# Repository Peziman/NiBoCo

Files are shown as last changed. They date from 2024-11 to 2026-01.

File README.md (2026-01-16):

# NiBoCo
Boardcomputer and controller for a CWA pump for my Nissan Micra GA16DE project

# Why
I installed a GA16DE engine from a Nissan Almera in a Nissan Micra K11 1.0. Since this engine is much larger, there was no room for the V-belt drive of the water pump. Cutting out the frame was not an option for me, so the cooling system had to be converted to an electric pump. I chose a Pierburg CWA200 water pump, which is installed in some BMWs.

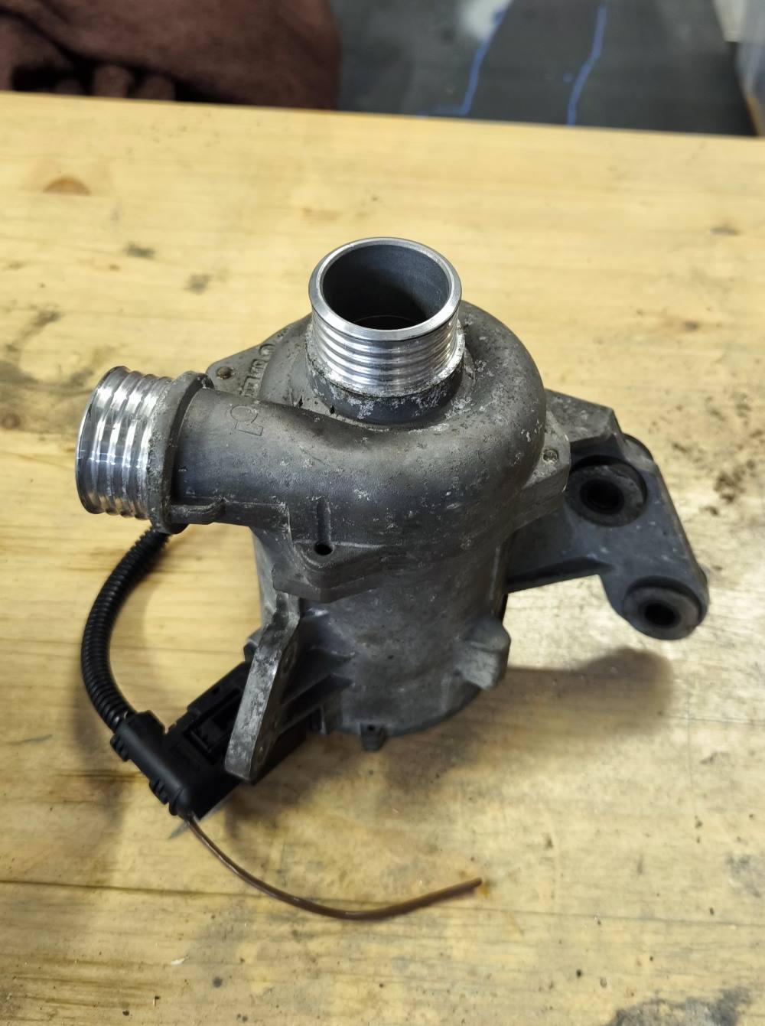
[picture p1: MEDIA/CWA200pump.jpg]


I also wanted to have an additional display in my speedometer for my Speeduino.
MielArrojado's project "speeduino-ardugauge" is just perfect.

https://github.com/MielArrojado/speeduino-ardugauge

So why not combine the two?

**This is a standalone version! There's no connection to Speeduino!**

# How is the cooling system set up?

Since there was no room for the belt drive of the water pump due to space constraints, and cutting into the frame for legal reasons was avoided, an electric coolant pump from BMW, an external thermostat from a Fiat 126, and a VW secondary pump for the heating circuit are used.

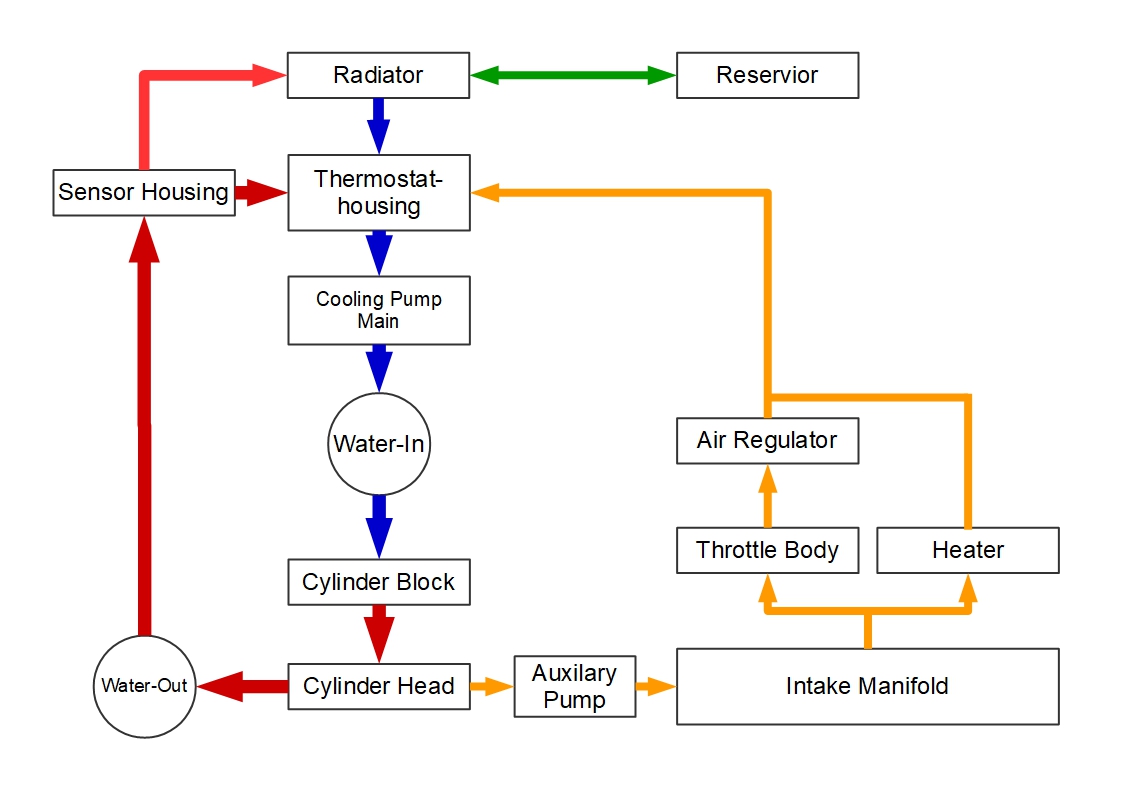
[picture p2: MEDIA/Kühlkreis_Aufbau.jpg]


The system is controlled by an Arduino Nano and a bit of chicken feed.

The CWA200 main pump is controlled via a PWM (pulse width modulation) signal.
The secondary pump is also controlled via a PWM signal.

The speed and the corresponding flow rate are regulated directly by the coolant temperature. Visual feedback is provided via a display and an RGB LED in the instrument cluster. The control points can be adjusted using two potentiometers.

The radiator fan is also controlled by the controller.

# How is it regulated?

Temperature control is achieved via a total of 4 different temperature programs,
which are referred to as modes below. The currently active mode is indicated by the LED in the instrument cluster.

The system regulates to a target temperature (e.g., 85°C).

### Mode 1 (Warm-Up Pulse Mode)

If the coolant temperature is less than 25°C below the target temperature (60°C), the engine speed switches between an absolute minimum value of 10% (350 rpm) and the predefined lower reference point, which is set via the "Reference Low" potentiometer (e.g., 30%).

The pump then runs for 30 seconds at 10% speed and 4 seconds at 30% speed.

The secondary pump runs at approximately 60% speed.

This ensures a clean and rapid warm-up of the engine.

As feedback, the LED in the instrument cluster illuminates blue.

### Mode 2 (Warm-Up)

When the coolant temperature is between 25°C and 10°C below the target temperature (60°C-75°C), the pump speed is maintained at the predefined lower reference point.

The secondary pump is continuously ramped up to 100%.

As feedback, the LED in the instrument cluster lights up turquoise.

### Mode 3 (Normal Operation)

When the coolant temperature is higher than 10°C below the target temperature, the pump speed is controlled by a PID-styled controller.

The maximum operating speed can be set using the potentiometer "Reference High" (e.g., 90%).

The PID controller attempts to maintain the temperature at 85°C by adjusting the pump speed.

The secondary pump continues to run at 100%.

As feedback, the LED in the instrument cluster lights up green.

### Mode 4 (Overheating)

If the coolant temperature exceeds 98°C (target temperature +13°C), the speed of
both pumps is set to 100% to counteract further overheating.

This pump behavior also occurs if the connection to the pump is interrupted. (Fail-Safe Mode)
As feedback, the LED in the instrument cluster lights up red.

## Fan Control
At a set temperature of 90°C, the radiator fan is activated.

The hysteresis is 4°C.

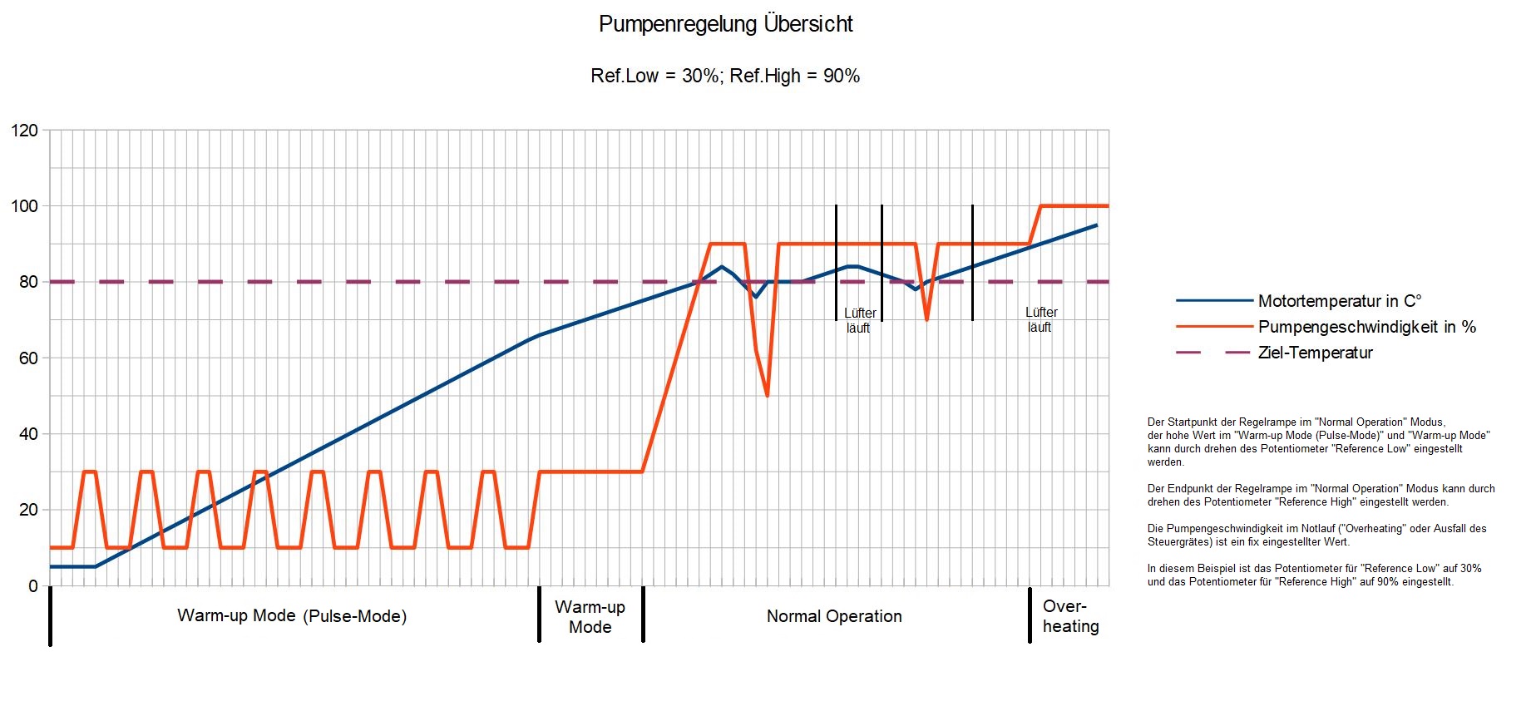
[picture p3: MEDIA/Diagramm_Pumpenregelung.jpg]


## Afterrun control

When the ignition is switched off, the pump does not switch off immediately but continues to monitor the coolant temperature.

If the temperature is within the Mode 3 range, the pump continues to run for another 60 seconds to prevent potential hot spots in the engine.

# What else can it do?

The display also shows water temperature, oil temperature, vehicle voltage, pump status, and a few bit indicators.

It's located in the instrument cluster in place of the clock.

Operation is via three pushbuttons, which were originally intended for the clock (forward, back, enter).

The display has the following pages:

### Page 1:

Oil and water temperature display

### Page 2:

Vehicle voltage display

### Page 3:

Main pump status, such as setpoints, current speed, etc.

### Page 4:

Various indicators, such as fan running, after-run active, sensor fault, etc.

### Page 5:

Auxiliary pump status, such as setpoints, current speed, etc.

### Page 6:
Frames per second

Additionally, alarm messages are displayed when limit values are exceeded.

By pressing and holding the Enter key, you can switch to a kind of test mode to manually control the pumps and fans.

# What's next?

Since this project has been working flawlessly in my car for 1.5 years, I consider it complete.

I might add an oil pressure sensor, but will that ever happen? We'll see what the future holds.

Feel free to build your own.

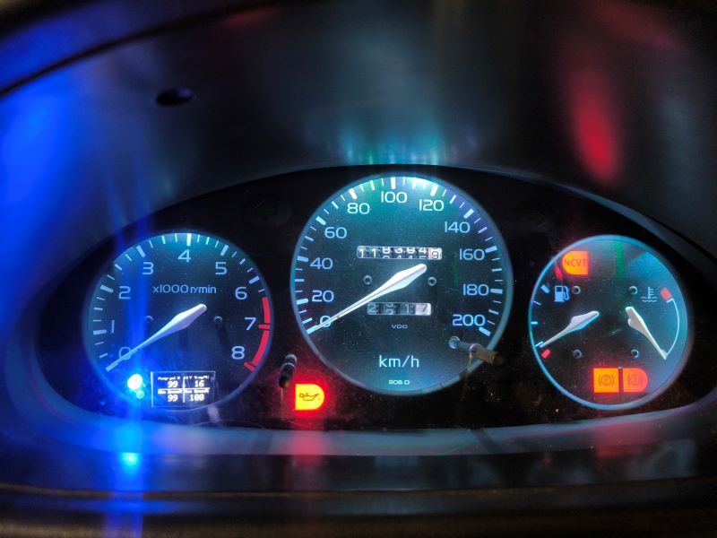
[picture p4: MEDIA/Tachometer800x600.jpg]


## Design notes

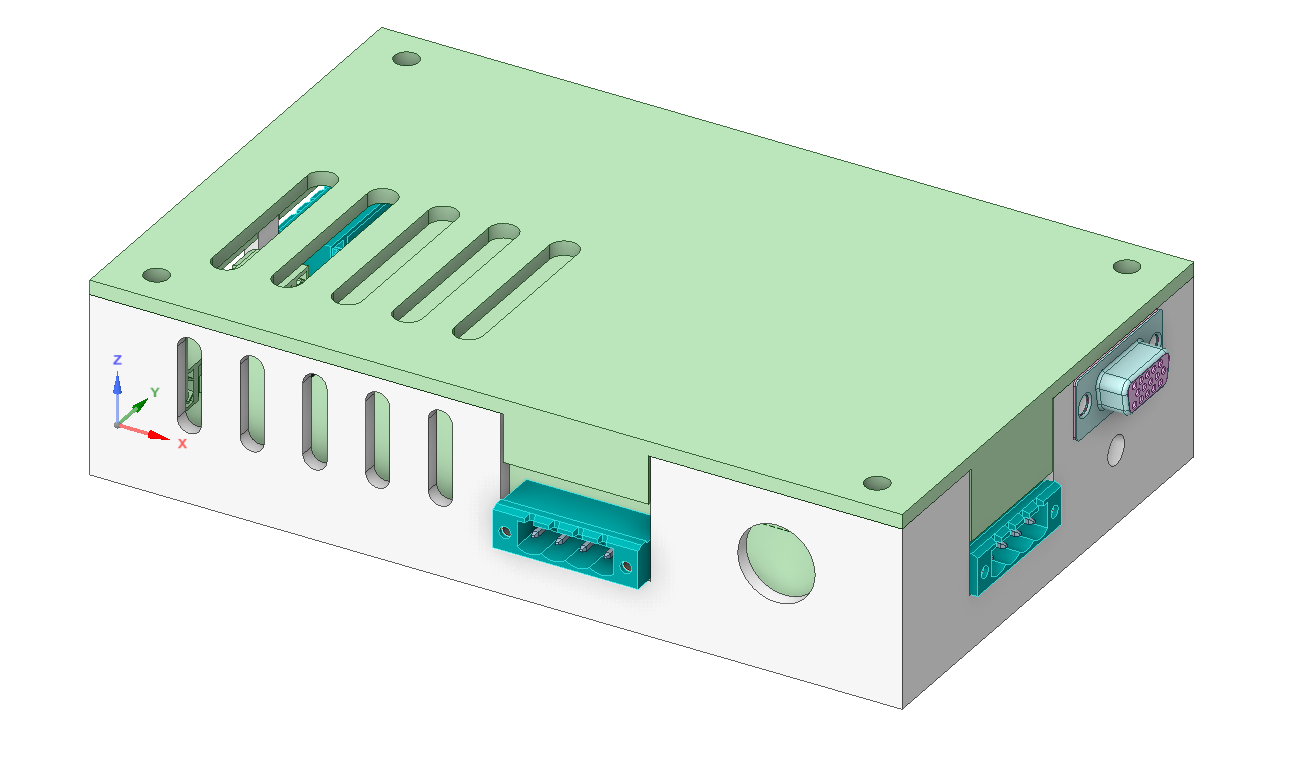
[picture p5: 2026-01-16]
Hardware/NiBoCo Gehäuse.png

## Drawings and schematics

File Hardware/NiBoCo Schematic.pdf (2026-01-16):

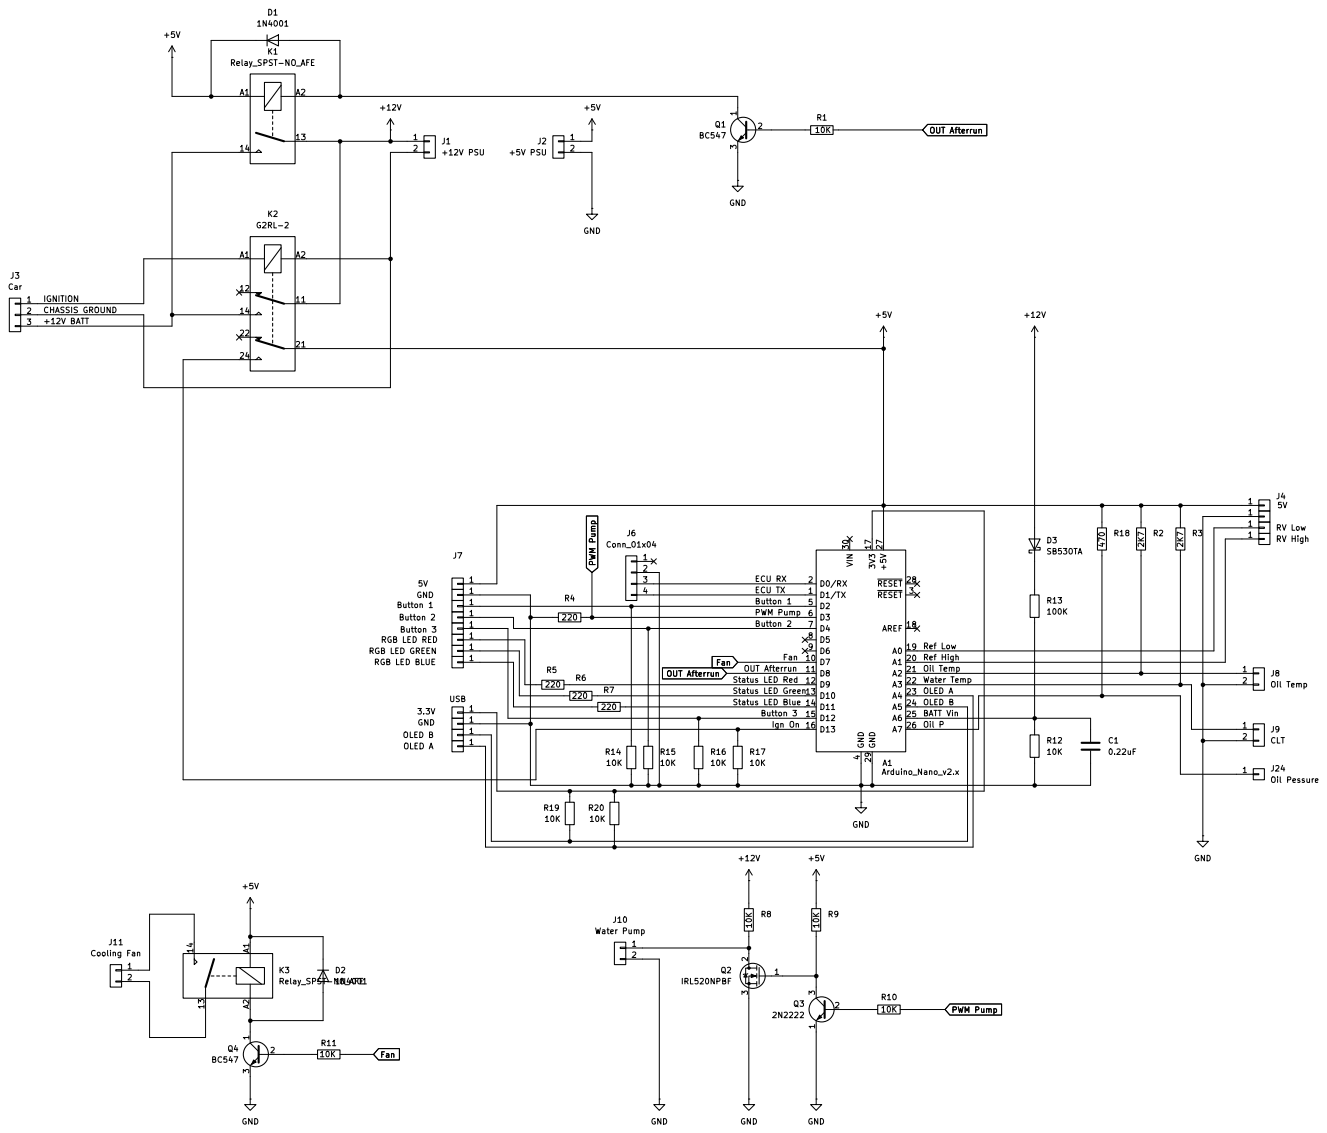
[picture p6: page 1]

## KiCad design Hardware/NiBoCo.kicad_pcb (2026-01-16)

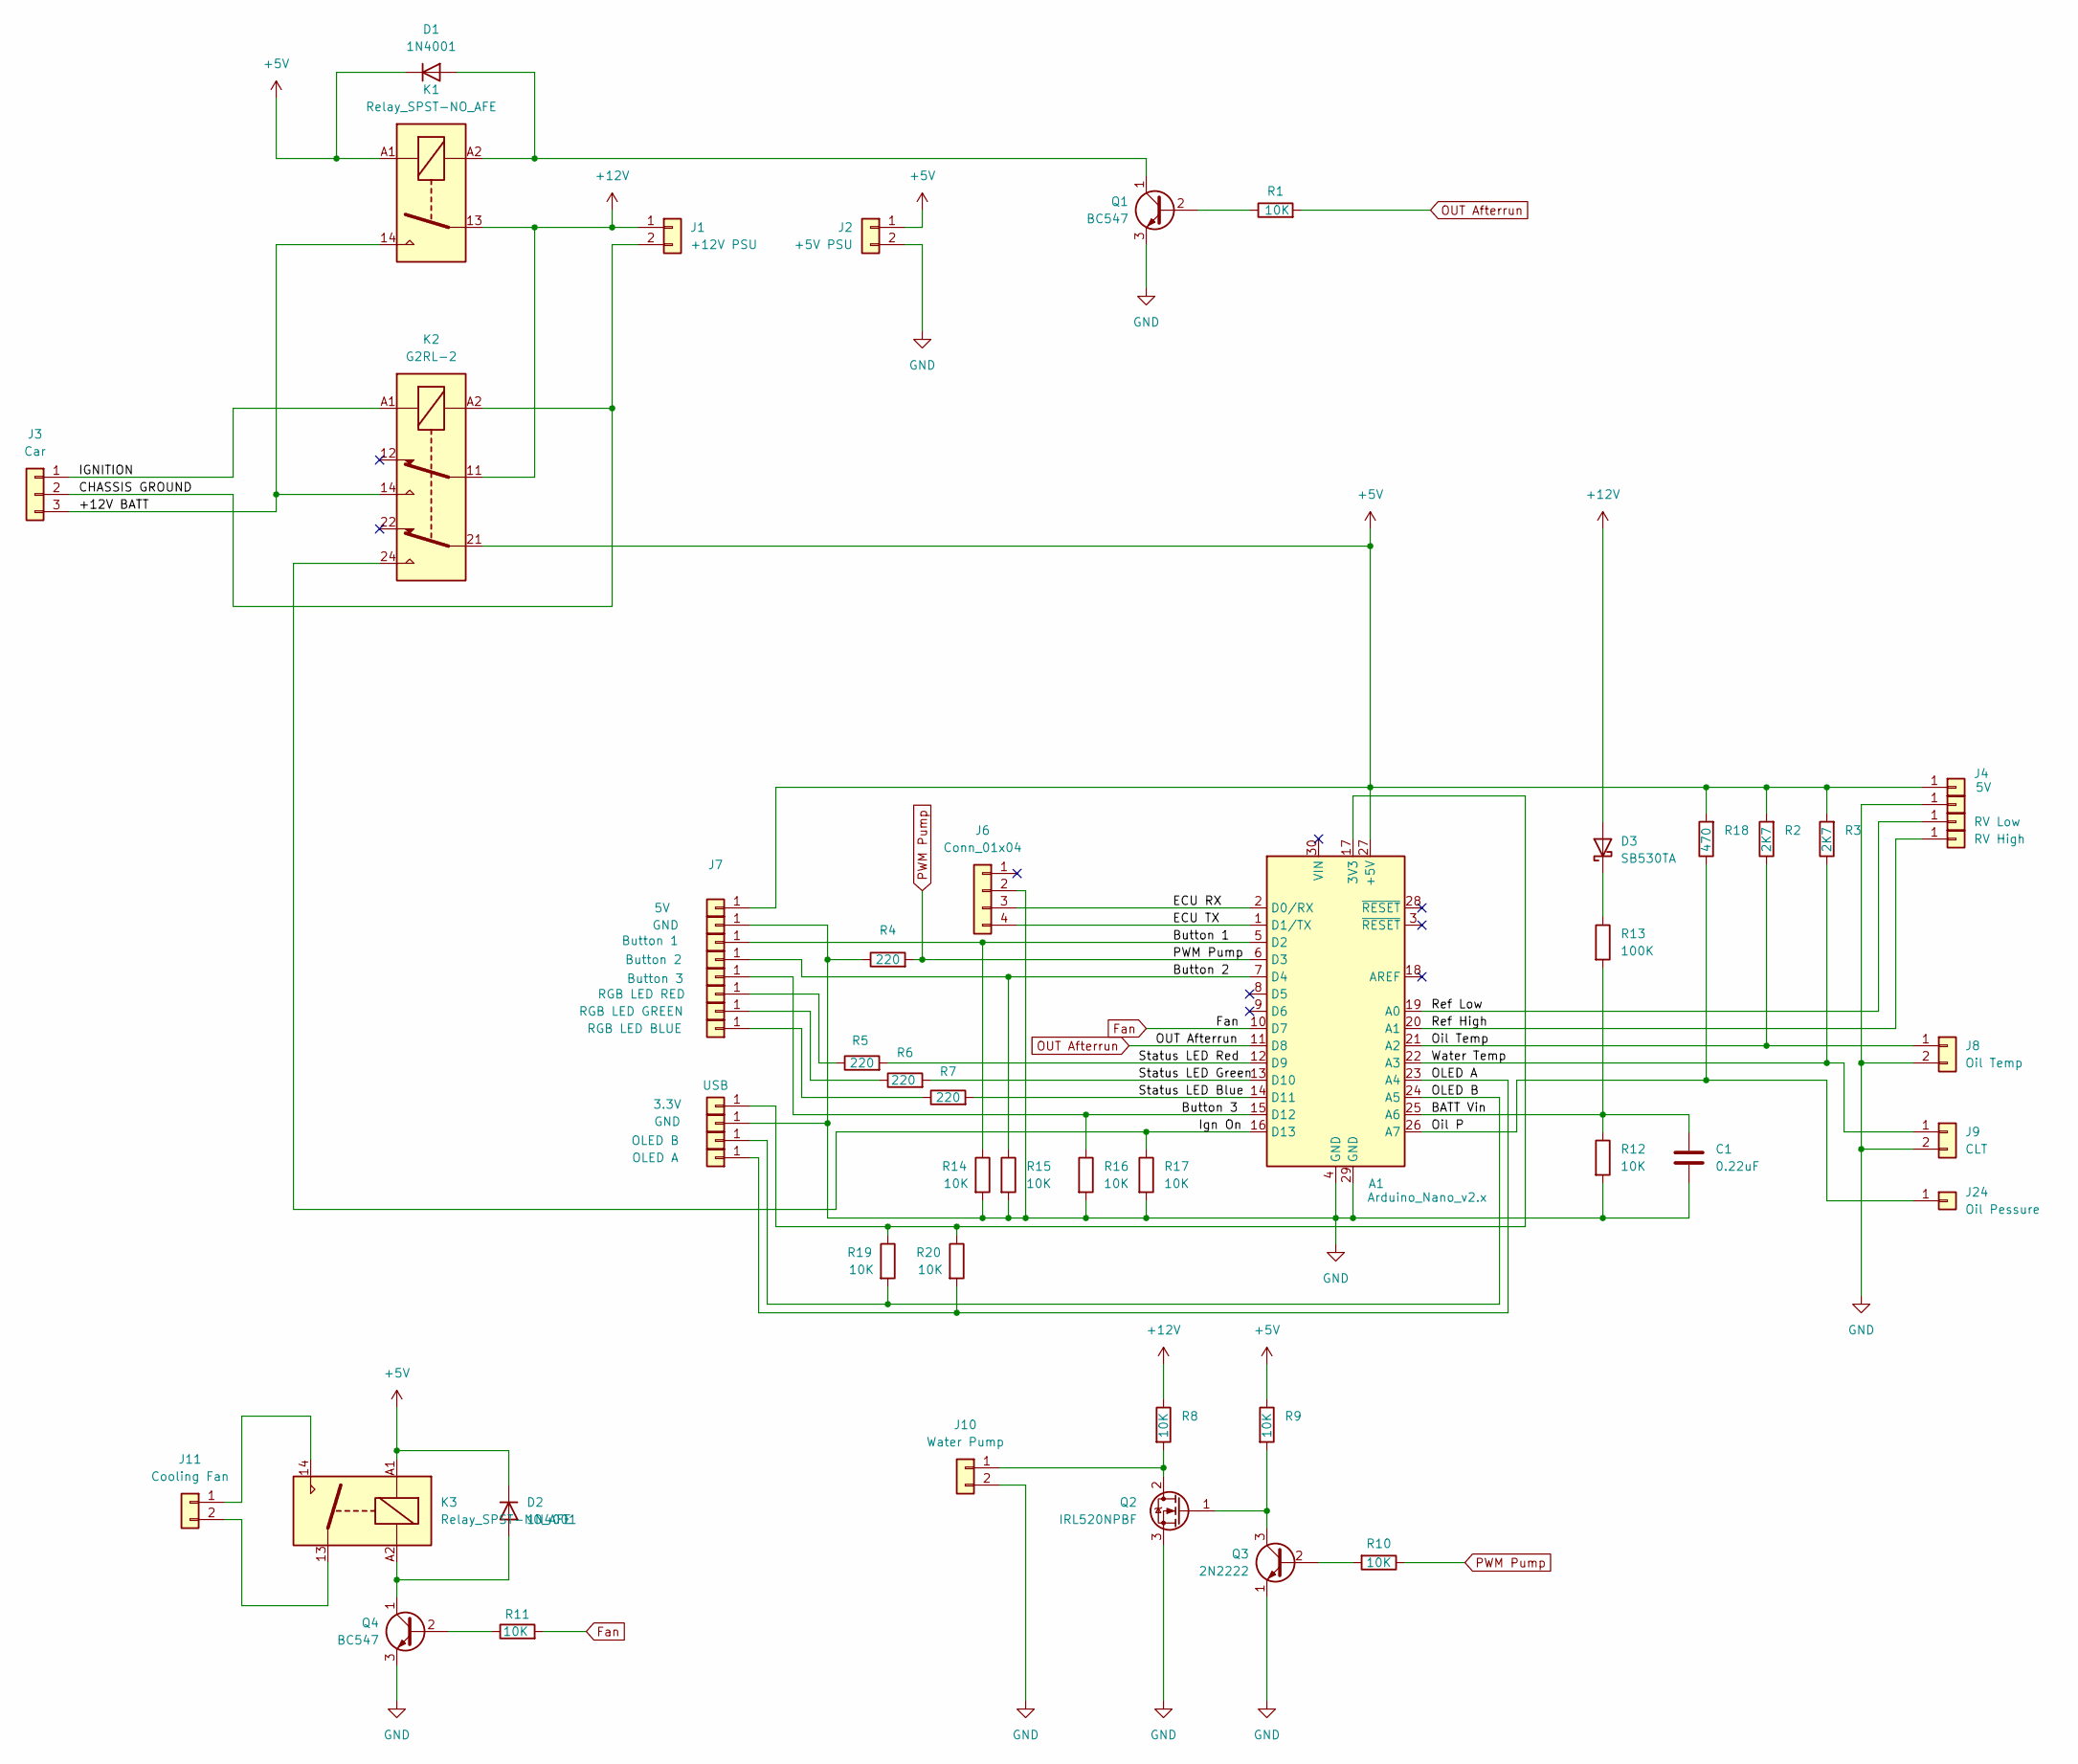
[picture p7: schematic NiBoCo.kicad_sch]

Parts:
A1: Arduino_Nano_v2.x; Arduino_Nano
C1: 0.22uF; C_Rect_L4.6mm_W4.6mm_P2.50mm_MKS02_FKP02
D1, D2: 1N4001; D_DO-41_SOD81_P10.16mm_Horizontal
D3: SB530TA; D_DO-201AD_P15.24mm_Horizontal
J1: +12V PSU; JST_NV_B02P-NV_1x02_P5.00mm_Vertical
J2: +5V PSU; JST_NV_B02P-NV_1x02_P5.00mm_Vertical
J3: Car; JST_NV_B03P-NV_1x03_P5.00mm_Vertical
J4, J7: 5V; TestPoint_Loop_D2.60mm_Drill1.4mm_Beaded
J5, J14, J21: GND; TestPoint_Loop_D2.60mm_Drill1.4mm_Beaded
J6: Conn_01x04; JST_NV_B04P-NV_1x04_P5.00mm_Vertical
J8: Oil Temp; JST_NV_B02P-NV_1x02_P5.00mm_Vertical
J9: CLT; JST_NV_B02P-NV_1x02_P5.00mm_Vertical
J10: Water Pump; JST_NV_B02P-NV_1x02_P5.00mm_Vertical
J11: Cooling Fan; JST_NV_B02P-NV_1x02_P5.00mm_Vertical
J12: RV Low; TestPoint_Loop_D2.60mm_Drill1.4mm_Beaded
J13: RV High; TestPoint_Loop_D2.60mm_Drill1.4mm_Beaded
J15: Button 1; TestPoint_Loop_D2.60mm_Drill1.4mm_Beaded
J16: Button 2; TestPoint_Loop_D2.60mm_Drill1.4mm_Beaded
J17: Button 3; TestPoint_Loop_D2.60mm_Drill1.4mm_Beaded
J18: RGB LED RED; TestPoint_Loop_D2.60mm_Drill1.4mm_Beaded
J19: RGB LED GREEN; TestPoint_Loop_D2.60mm_Drill1.4mm_Beaded
J20: RGB LED BLUE; TestPoint_Loop_D2.60mm_Drill1.4mm_Beaded
J22: OLED B; TestPoint_Loop_D2.60mm_Drill1.4mm_Beaded
J23: OLED A; TestPoint_Loop_D2.60mm_Drill1.4mm_Beaded
J24: Oil Pessure
K1, K3: Relay_SPST-NO_AFE; Relay_SPST_Zettler-AZSR131
K2: G2RL-2; Relay_DPDT_Omron_G2RL-2
Q1, Q4: BC547; TO-92_Inline
Q2: IRL520NPBF; TO-220-3_Vertical
Q3: 2N2222; TO-39-3
R1, R8, R9, R10, R11, R12, R14, R15, R16, R17, R19, R20: 10K; R_Axial_DIN0204_L3.6mm_D1.6mm_P5.08mm_Horizontal
R2, R3: 2K7; R_Axial_DIN0204_L3.6mm_D1.6mm_P5.08mm_Horizontal
R4, R5, R6, R7: 220; R_Axial_DIN0204_L3.6mm_D1.6mm_P5.08mm_Horizontal
R13: 100K; R_Axial_DIN0204_L3.6mm_D1.6mm_P5.08mm_Horizontal
R18: 470; R_Axial_DIN0204_L3.6mm_D1.6mm_P5.08mm_Horizontal
USB: 3.3V; TestPoint_Loop_D2.60mm_Drill1.4mm_Beaded

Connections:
+5V: A1.27 (+5V), D1.1 (K), D2.1 (K), J2.1, J4.1, J7.1, K1.A1, K2.21, K3.A1, R2.2, R3.2, R9.1, R18.2
+12V: D3.2 (A), J1.1, K1.13, K2.11, R8.1
/+12V BATT: J3.3, K1.14, K2.14
/BATT Vin: A1.25 (A6), C1.1, R12.1, R13.2
/Button 1: A1.5 (D2), J15.1, R14.1
/Button 2: A1.7 (D4), J16.1, R15.1
/Button 3: A1.15 (D12), J17.1, R16.1
/CHASSIS GROUND: J1.2, J3.2, K2.A2
/ECU RX: A1.2 (D0/RX), J6.3
/ECU TX: A1.1 (D1/TX), J6.4
/IGNITION: J3.1, K2.A1
/Ign On: A1.16 (D13), K2.24, R17.1
/OLED A: A1.23 (A4), J23.1, R20.2
/OLED B: A1.24 (A5), J22.1, R19.2
/Oil Temp: A1.21 (A2), J8.1, R2.1
/Ref High: A1.20 (A1), J13.1
/Ref Low: A1.19 (A0), J12.1
/Status LED Blue: A1.14 (D11), R7.2
/Status LED Green: A1.13 (D10), R6.2
/Status LED Red: A1.12 (D9), R5.2
/Water Temp: A1.22 (A3), J9.1, R3.1
Fan: A1.10 (D7), R11.2
GND: A1.4 (GND), A1.29 (GND), C1.2, J2.2, J5.1, J6.2, J8.2, J9.2, J10.2, J14.1, J21.1, Q1.3 (E), Q2.3 (S), Q3.1 (E), Q4.3 (E), R4.1, R12.2, R14.2, R15.2, R16.2, R17.2
unnamed: D1.2 (A), K1.A2, Q1.1 (C)
unnamed: D2.2 (A), K3.A2, Q4.1 (C)
unnamed: D3.1 (K), R13.1
unnamed: J10.1, Q2.2 (D), R8.2
unnamed: J11.1, K3.14
unnamed: J11.2, K3.13
unnamed: J18.1, R5.1
unnamed: J19.1, R6.1
unnamed: J20.1, R7.1
unnamed: A1.26 (A7), J24.1, R18.1
unnamed: Q1.2 (B), R1.1
unnamed: Q2.1 (G), Q3.3 (C), R9.2
unnamed: Q3.2 (B), R10.2
unnamed: Q4.2 (B), R11.1
unnamed: A1.17 (3V3), R19.1, R20.1, USB.1
OUT Afterrun: A1.11 (D8), R1.2
PWM Pump: A1.6 (D3), R4.2, R10.1

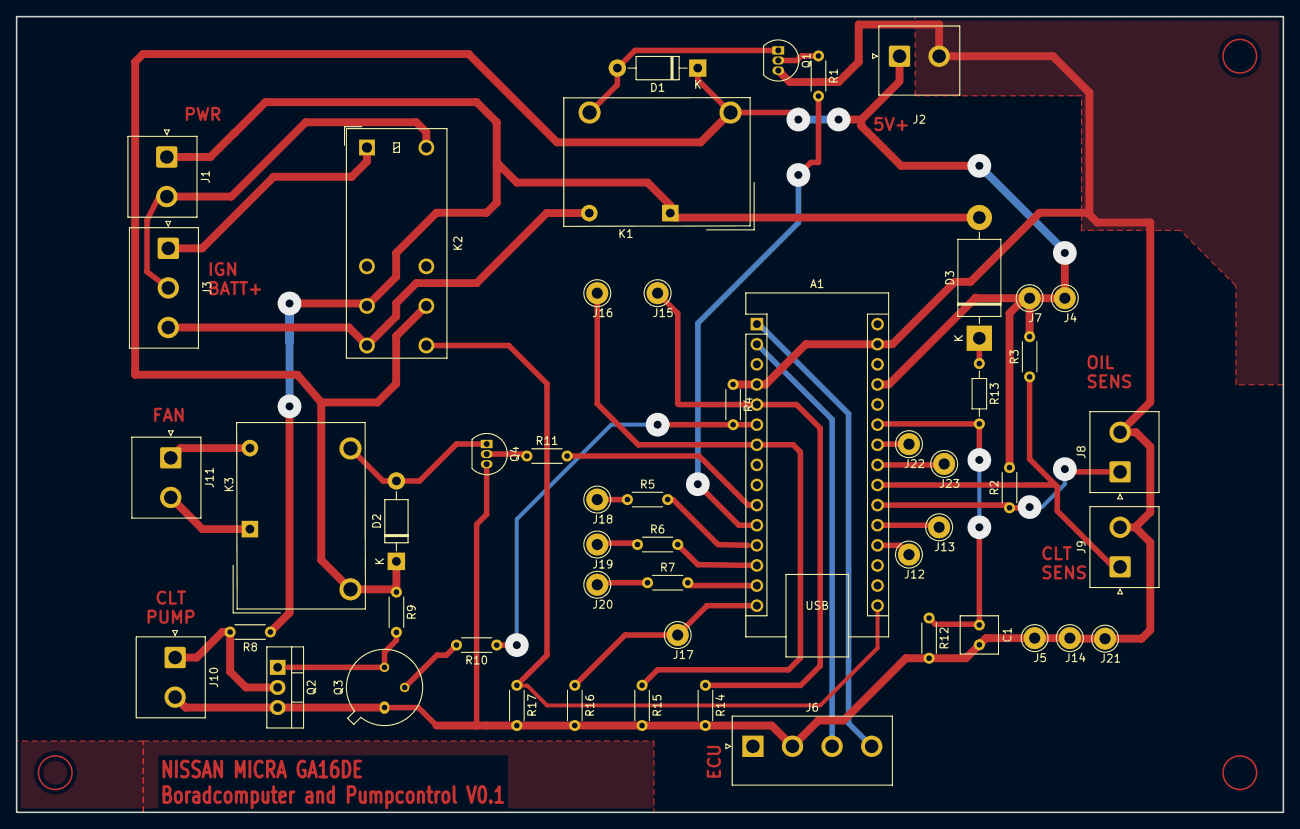
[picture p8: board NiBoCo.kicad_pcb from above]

Board: 2 copper layers, 160.0 x 100.5 mm, 52 parts (0 on the bottom side), 38 nets.

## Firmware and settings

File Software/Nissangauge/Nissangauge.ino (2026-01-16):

#include "Arduino.h"
#include "Pages.h"
#include "Pump_control.h"
#include "Nissangauge.h"

const float diodeVoltage = 0.538;  // forward voltage of the used diode in Volts
const float R1 = 98500.0;          // exact resistance of R1 (= 100 kOhm)
const float R2 = 9410.0;           // exact resistance of R2 (= 10 kOhm)

uint8_t pageNum = 0;
bool test_mode = false;
uint8_t ticks = 0;

void setup() {
  Serial.begin(9500);
  initDisplay();
  if (pageNum >= N_PAGES) {
    pageNum = 0;
  }
  initPump();
  pinMode(Btn_next, INPUT);
  pinMode(Btn_prev, INPUT);
  pinMode(Btn_push, INPUT);
  pinMode(BATT_RAW, INPUT);
}

void tik_tak()
{
  if (ticks > 255)
  {
    ticks = 0;
  }
  else
  {
    ticks++;
  }
}


uint16_t get_VOLT()
{
  float vout = 0.0;
  float BATT_V = 0.0;
  uint16_t BATT_V2 = 0;
  uint16_t rawValue = 0;
  rawValue = analogRead(BATT_RAW);
  vout = (rawValue * REF_VOLTAGE) / PIN_STEPS;
  BATT_V = vout / (R2 / (R1 + R2)) * 10;
  BATT_V = BATT_V + diodeVoltage;
  BATT_V2 = (uint16_t)BATT_V;
  return BATT_V2;
}


void fail_check()
{
  if (get_overtemp() == true && ticks == 1)
  {
    pageNum = 11;
  }
  if (getOilTemp() > 135 && ticks == 100)
  {
    pageNum = 12;
  }
  if (get_VOLT() > 1500 || get_VOLT() < 110 && ticks == 200)
  {
    pageNum = 13;
  }
  //Serial.println(get_VOLT());
}

void loop() {

  // button and page number operations
  static bool buttonLast = false;
  static bool buttonHeld = false;
  static uint32_t timePressed = 0;
  //static uint8_t oilTemp = 0;
  //static uint8_t cltTemp = 0;


  static bool btn_nextNow = digitalRead(Btn_next);
  static bool btn_prevNow = digitalRead(Btn_prev);
  static bool btn_pushNow = digitalRead(Btn_push);
  static bool btn_nextHIGH = false;
  static bool btn_prevHIGH = false;
  static bool btn_pushHIGH = false;
  //digitalWrite(LED_BUILTIN, btn_nextNow);



  //button Next pressed

  if (digitalRead(Btn_next) == true) 
  {
    btn_nextHIGH = true;
  }
  if (digitalRead(Btn_next) == false && btn_nextHIGH == true) 
  {
    if (test_mode == false)
    {
      pageNum++;
      if (pageNum >= N_PAGES)
        pageNum = 0;
      btn_nextHIGH = false;
    }
  }

  //button Prev pressed

  if (digitalRead(Btn_prev) == true)  
  {
    btn_prevHIGH = true;
  }
  if (digitalRead(Btn_prev) == false && btn_prevHIGH == true)
  {
    if (test_mode == false)
    {
      pageNum--;
      if (pageNum >= N_PAGES)
        pageNum = N_PAGES - 1;   
      btn_prevHIGH = false;
    }
  }


  //button Enter pressed

  if (digitalRead(Btn_push) == true && btn_pushHIGH == false)
  {
    btn_pushHIGH = true;
    timePressed = millis();
  }
  
  if (digitalRead(Btn_push) == false && btn_pushHIGH == true) 
  {
    Serial.println(millis() - timePressed);
    if ((millis() - timePressed) > BUTTON_HOLD_TIME)
    {
      if (test_mode == false)
      {
        test_mode = true;
        testmode_init();
        pageNum = 10;
      }
      else
      {
        test_mode = false;
        pageNum = 0;
      }
    }
    else
    {
      if (test_mode == false)
      {
        pageNum++;
        if (pageNum >= N_PAGES)
          pageNum = 0;
      }
    }
    btn_pushHIGH = false;
  }

  // serial operation, frequency based request
  static uint32_t lastUpdate = millis();
  if (millis() - lastUpdate > SERIAL_UPDATE_MS) {
    lastUpdate = millis();
    if (test_mode == true)
    {
      testmode();
    }
    else
    {
      runPump();
      Fan();
      afterrun_control();
      tik_tak();
      fail_check();
    }
    //oilTemp = getOilTemp();
    //cltTemp = getCLTTemp();

  }

  // get refresh rate
  static uint32_t lastRefresh = millis();
  uint16_t refreshRate = 1000 / (millis() - lastRefresh);
  lastRefresh = millis();

  // display pages
  switch (pageNum) {
    case 0:
      show2Bar(F("Water Temperatur (\367C)"), getCLTTemp(), 0, 120, 0,
               F("Oil Temperatur (\367C)"), getOilTemp(), 0, 150, 0);
      //showBar(F("Engine Speed (RPM)"), getWord(14), 0, 6000);
      break;
    case 1:
      showBar(F("Battery (V)"), get_VOLT(), 60, 160, 1);
      break;
    case 2:
      show4Numeric(F("Pumpspd %"), get_pump_duty(), 0, 100, 0,
                   F("CLT Temp\367C"), getCLTTemp(), 0, 120, 0,
                   F("Min Speed%"), get_pot_duty(0), 0, 100, 0,
                   F("Max Speed%"), get_pot_duty(1), 0, 100, 0);
      break;
    case 3:
      showFlags(F("Fan"), get_fan_state(),
                F("RUN"), get_ign_state(),
                F("AFTERRUN"), get_afterrun(),
                F("warm"), get_warmup(),
                F("CLT ERROR"), get_Temp_sens_state(getCLTTemp()),
                F("OIL Error"), get_Temp_sens_state(getOilTemp()),
                F(""), false,
                F(""), false);
      //showBar(F("Coolant Temp (\367C)"), (int16_t)getByte(7) - 40, 0, 120);
      break;
    case 4:
      show2Bar(F("AUX Pumpspeed %"), get_aux_duty(), 0, 100, 0,
               F("Water Temperatur (\367C)"), getCLTTemp(), 0, 120, 0);
      break;
    case 5:
      showNumeric(F("FPS"), refreshRate, 0, 100, 0);
      break;  
    case 10:
      show4Numeric(F("Pumpspd %"), get_pump_duty(), 0, 100, 0,
                   F("AUX Pump %"), get_aux_duty(), 0, 100, 0,
                   F("Lower Pot %"), test_pot_duty(0), 0, 100, 0,
                   F("Top Pot %"), test_pot_duty(1), 0, 100, 0);
      break;
    case 11:
      showBar(F("CLT Temp\367C FAIL"), getCLTTemp(), 0, 120, 0);
      break;  
    case 12:
      showBar(F("OIL Temp\367C FAIL"), getOilTemp(), 0, 150, 0);
      break;
    case 13:
      showBar(F("Battery (V) FAIL"), get_VOLT(), 60, 160, 1);
      break;      
    default:
      showSplash(F("Coming Soon!"));
      break;
  }
}

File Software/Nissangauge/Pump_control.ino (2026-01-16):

#include "Arduino.h"
#include "Pump_control.h"
#include "Pages.h"


bool after_run = false;
bool warm_dis = false;
uint8_t get_CLT = 0;
uint8_t pump_duty = 0;
uint8_t aux_duty = 0;
bool fan_on = false;
int16_t PID;
//uint16_t auxspeed_2 = 0;

void initPump() 
{
  //declare Pins
  pinMode(Out_pump_pwm, OUTPUT);
  pinMode(Out_led_r, OUTPUT);
  pinMode(Out_afterrun_on, OUTPUT);
  pinMode(Out_fan, OUTPUT);

  pinMode(In_run, INPUT);
  
  //pump start up see CWA200 pump docs
  // simulate LIN-Bus commands to wakeup and setup PWM mode 
  analogWrite(Out_pump_pwm, 0); //100% PWM Pumpspeed
  digitalWrite(Out_led_r, HIGH); //LED indicator
  delay(300); //for 300ms
  analogWrite(Out_pump_pwm, 255);
  digitalWrite(Out_led_r, LOW); //LED indicator
  delay(100); //wait 100ms before reset pump
  analogWrite(Out_pump_pwm, 229); // 10% duty cycle to reset it
  digitalWrite(Out_led_r, HIGH); //LED indicator
  delay(300); // for 300ms
  analogWrite(Out_pump_pwm, 255);
  digitalWrite(Out_led_r, LOW); //LED indicator
  delay(10);
  
}

uint16_t get_pot(uint8_t a_input, uint8_t pwm1, uint8_t pwm2) // get values from the desired potentiometer
{
  uint16_t sensorValue;
  sensorValue = map(analogRead(a_input), 0, 1023, pwm1, pwm2);
  return sensorValue;
}

uint16_t get_pot_duty(uint8_t a_input) //for display return the current position of potentiometer
{
  uint16_t high_pot_duty;
  uint16_t low_pot_duty;
  low_pot_duty = map(analogRead(In_low_ref), 0, 1023, 100 * (lowspeed - no_speed)/(max_speed - no_speed), 100 * (hot_speed - no_speed)/(max_speed - no_speed));
  high_pot_duty = map(analogRead(In_high_ref), 0, 1023, low_pot_duty, 100);

  if (a_input == false)
  {
    return low_pot_duty;
  }
  else
  {
    return high_pot_duty;
  }
}

uint16_t test_pot_duty(uint8_t a_input) //for display return the current position of potentiometer in testmode
{
  uint16_t high_pot_duty_t;
  uint16_t low_pot_duty_t;
  low_pot_duty_t = map(analogRead(In_low_ref), 0, 1023, 0, 100);
  high_pot_duty_t = map(analogRead(In_high_ref), 0, 1023, 0, 100);

  if (a_input == false)
  {
    return low_pot_duty_t;
  }
  else
  {
    return high_pot_duty_t;
  }
}


uint8_t get_pump_duty() //for display return the current  duty of the pump
{
  return pump_duty;    
}

uint8_t get_aux_duty() //for display return the current  duty of the auxpump
{
  return aux_duty;    
}

bool get_fan_state() //for display get the actually state of the cooling fan
{
  if (digitalRead(Out_fan) == true)
  {
    return 1;
  } 
  else
  { 
    return 0;
  } 
}

bool get_afterrun() // for display get the state of the after run output 
{
  return after_run;
}

bool get_ign_state() // for display get the state of the engine is running 
{
  if (digitalRead(In_run) == true)
  {
    return 1;
  }
  else
  {
    return 0;
  }
}

bool get_warmup() // for display return the state of the warmup mode
{
  return warm_dis;
}

bool get_overtemp()
{
  if (get_CLT > target_temp + over_temp)
  {
    return true;
  }
  else
  {
    return false;
  }
}

bool get_Temp_sens_state(uint8_t Temp) //for display return if a temp sensor is damaged or not connected 
{
  if (Temp == 255)
  {
    return true;
  }
  else
  {
    return false;
  }
}



void runPump()
{
  static bool pumpPause = false; 
  static bool pumpRun = false; 
  static uint32_t pumpTime = 0;
  static bool warm_up = false;
  static bool overheat = false;
  static uint8_t add_rpm = 0;
  static uint8_t add_tps = 0;
  uint16_t get_coldspeed;
  uint16_t get_warmspeed;
  uint8_t p_value;
  uint8_t led_value;
  
   
  uint16_t get_CLT = GETDATA(0); 

 
  if (get_CLT <= target_temp - heatup_temp & get_CLT <= target_temp - heatup_temp2 && overheat == false)
  {      
    //warm up stage 1
    // cold engine
    // pump switch between 2 states (absolutely min rpm and the value of the Ref min potentiometer)  
    // the RGB status Led shows blue     
    warm_up = true;
    after_run = false;
    overheat = false;
    warm_dis = true;
    PID = get_PWM(0,0,0,false);
    analogWrite(Out_led_g, 0); 
    digitalWrite(Out_led_r, LOW);
    digitalWrite(Out_afterrun_on, LOW);
    set_auxspeed(aux_low, 3);
    
    if (pumpTime == 0) 
    {
      pumpTime = millis();      
    } 
    
    if (pumpRun == false & ((millis() - pumpTime) <= lowspeed_time)) 
    {
      //lowspeed
      set_pumpspeed(lowspeed);
      analogWrite(Out_led_b, led_b_min);      
    }
    else if (pumpRun == false & ((millis() - pumpTime) > lowspeed_time)) 
    {
      //switch to highspeed
      pumpTime = 0; 
      pumpRun = true;
      pumpTime = millis();
    }  
    else if (pumpRun == true & ((millis() - pumpTime) <= highspeed_time))
    {
      //highspeed
      get_coldspeed = get_pot(In_low_ref, lowspeed, hot_speed);
      set_pumpspeed(get_coldspeed);
      analogWrite(Out_led_b, led_b_max);             
    } 
    else if (pumpRun == true & ((millis() - pumpTime) > highspeed_time))
    {
      //switch to lowspeed
      pumpTime = 0;
      pumpRun = false;
      pumpTime = millis();
    }          
     
  }
  else if (get_CLT < target_temp - heatup_temp2 & get_CLT > target_temp - heatup_temp)
  {
    //warm up stage 2
    //engine is bit warmer
    //pump runs on the value of the Ref min potentiometer
    //the RGB status Led shows turkis
    analogWrite(Out_led_b, led_b_min);
    analogWrite(Out_led_g, led_g_s2);
    digitalWrite(Out_led_r, LOW);
    digitalWrite(Out_afterrun_on, LOW);
    warm_up = true;
    overheat = false;
    warm_dis = false;
    after_run = false;
    PID = get_PWM(0,0,0,false);
    get_coldspeed = get_pot(In_low_ref, lowspeed, hot_speed);
    set_pumpspeed(get_coldspeed);
    set_auxspeed(aux_norm, 3);
  }  

  else if (get_CLT >= target_temp - heatup_temp2 & get_CLT < target_temp + over_temp)  
  {
    // normal operation  
    // pump runs depending on engine coolant temperature (min and max speeds are given by the ref min and ref max potentionmeter)
    // the RGB staus Led shows the current duty cycle of this mode
    warm_up = false;
    overheat = false;
    warm_dis = false;
    after_run = true;
    add_rpm = 0; //GETDATA(1);
    add_tps = 0; //GETDATA(2);
    analogWrite(Out_led_b, 0); 
    digitalWrite(Out_led_r, LOW);
    digitalWrite(Out_afterrun_on, HIGH); 
    get_coldspeed = get_pot(In_low_ref, lowspeed, hot_speed);
    get_warmspeed = get_pot(In_high_ref, get_coldspeed, max_speed);
    //p_value = map(get_CLT, 63, 90, 50, 200);
    p_value = get_PWM(get_CLT, get_coldspeed, get_warmspeed, true);
    //p_value = constrain(map(get_CLT, target_temp - heatup_temp2, target_temp, get_coldspeed, get_warmspeed), lowspeed, get_warmspeed);
    
    // for future add speed at some conditions of driving
    if (add_rpm > rpm_limit)
    {
      p_value = p_value + add_rpm_v;
    }
    if (add_tps > tps_limit) 
    {
      p_value = p_value + add_tps_v;
    }
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

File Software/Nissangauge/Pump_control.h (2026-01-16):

//#ifndef PUMP_CONTROL_H
#define PUMP_CONTROL_H

#include "Arduino.h"

//INPUT//

#define In_low_ref A1 //ref Potentiometer specific Minimum pump speed
#define In_high_ref A0 //ref Potentiometer specific Maximum pump speed
#define In_run 13 //Input Pin Ignition for afterrun function

//Output//

#define Out_led_r 9 //Output Pin contorl LED Red
#define Out_led_g 11 //Output Pin contorl LED Green
#define Out_led_b 10 //Output Pin contorl LED Blue
#define Out_afterrun_on 8 //Output Pin power
#define Out_pump_pwm 3  //Output Pin CLT pump
#define Out_fan 7 //Output Pin cooling fan
#define Out_aux_pwm 5 //Output AUX pump PWM

//Temperatures//

#define heatup_temp 25  //temperatur  difference to target temperature (cold engine)
#define heatup_temp2 10  //temperatur  difference to target temperature (not so cold engine)
#define target_temp 85 //target cooling temperature
#define start_fan_diff_temp 7 //target_temp + start_fan_diff_temp = Fan strat temp
#define stop_fan_diff_temp 3 //target_temp + stop_fan_diff_temp = Fan stop temp
#define over_temp 13 //target_temp + start_fan_diff_temp = Start limpmode (Pump 100% Fan=On)

//Speeds
#define no_speed 36 //PWM value for 0% pumpspeed
#define hot_speed 215 //207 PWM 95% pumpspeed (for Limpmode or cooldown mode)
#define max_speed 216 //PWM 36-216 = 0-100% pumpspeed (limit maximum pumpspeed)
#define lowspeed 54 //PWM pump lowspeed 8% = 350rpm (limit minimum pumpspeed)
#define midspeed 126 //PWM pump speed 50% = 2250rpm (pumpspeed cooldown)
#define tps_limit 90 //TPS setpoint to add more flow
#define rpm_limit 6000 //RPM setpoint to add more flow
#define add_rpm_v 0 //PWM add RPM (Value added to pump speed when RPM limit is exceeded)
#define add_tps_v 0 //PWM add TPS (Value added to pump speed when TPS limit is exceeded)
#define aux_low 150 //PWM value for aux pump low speed
#define aux_norm 216  //PWM value for aux pump norm speed
#define aux_hot 255 //PWM value for aux pump hot speed
#define aux_min 90 //PWM value for aux pump absolute minimum speed


//times
#define lowspeed_time 30000 //pulse time warmupmode lowspeed (ms)
#define highspeed_time 4000 //pulse time warmupmode highspeed (ms)
#define afterrun_time 600 //time (1/10s) for afterrun when ignition off
#define blink_time 10 //time (1/10s) for additonal blink events

//PID constants
#define kp -50
#define ki -40
#define kd -130
#define i_loops 10 //1000ms
#define d_loops 50 //3000ms

//LED brightness
#define led_g_min 5   //5
#define led_g_max 50  //50
#define led_g_s2 15   //15
#define led_b_min 15   //15
#define led_b_max 25   //25


void initPump(); 
uint16_t get_pot(uint8_t a_input, uint8_t pwm1, uint8_t pwm2);
uint16_t get_pot_duty(uint8_t a_input);
uint16_t test_pot_duty(uint8_t a_input);
uint8_t get_pump_duty();
uint8_t get_aux_duty();
bool get_fan_state();
bool get_afterrun();
bool get_ign_state();

bool get_overtemp();
bool get_Temp_sens_state(uint8_t cltTemp);
void runPump();
void Fan();
bool afterrun_ok();
void afterrun_condition (bool (*condition)(void));
void afterrun_control();
void set_pumpspeed (uint8_t pumpspeed);
void set_auxspeed (uint8_t auxspeed);
uint16_t GETDATA (uint8_t x);
int16_t get_PWM (uint16_t clt, uint16_t low_point, uint16_t high_point, bool run);
void testmode_init();
void testmode();

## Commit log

2024-11-12 Update and rename Pump_control.h to Software/Nissangauge/Pump_control.h
2024-11-12 Update and rename Pump_control.ino to Software/Nissangauge/Pump_control.ino
2026-01-16 Rename Diagramm Pumpenregelung.jpg to Diagramm_Pumpenregelung.jpg
